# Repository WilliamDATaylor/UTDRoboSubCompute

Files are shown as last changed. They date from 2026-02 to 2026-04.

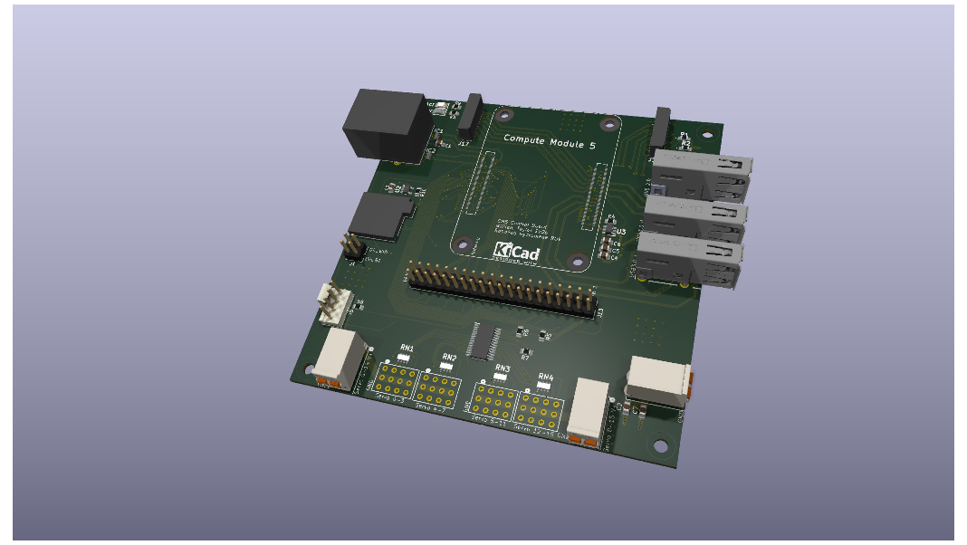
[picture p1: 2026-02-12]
UTDRoboSubCompute.png

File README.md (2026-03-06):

# UTDRoboSubCompute2026
Raspberry PI CM5 carrier board designed for the University of Texas at Dallas' ROV team, [RoboSub](https://utdrobosub.org/).

This will compete in the [2026 MateROV competition](https://materovcompetition.org/).

KiCad 3D render of the PCB

Kicad PCB View

Designs are heavily influenced by the reference RPI CM5 IO board.

[CM5 IO Board Datasheet](https://pip-assets.raspberrypi.com/categories/1097-raspberry-pi-compute-module-5-io-board/documents/RP-008182-DS-2-cm5io-datasheet.pdf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)

[CM5 IO Board KiCad Files](https://pip.raspberrypi.com/categories/1098-design-files)

[CM5 Datasheet](https://pip-assets.raspberrypi.com/categories/944-raspberry-pi-compute-module-5/documents/RP-008180-DS-6-cm5-datasheet.pdf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)

## Documentation Overview: 

### Table of Contents:

1. [Servo Controller](#servo-i2c-controller)
2. [GPIO Pins](#general-purpose-input-output-gpio)
3. [CSI/DSI](#csidsi-connectors)
4. [SD Card boot](#sd-cardtrans-flash-boot)
5. [Power Inputs](#power)
6. [USB 2.0](#usb-20)
7. [USB 3.0](#usb-30)
8. [CM5](#cm5)
9. [Fan](#fan)
10. [Sizing and dimensions](#sizing-and-dimensions)
11. [Trace Routing](#trace-routing)
12. [Additional Details](#additional-details)

### Servo (I<sup>2</sup>c) Controller: 
KiCad Schematic for Servo Controller

Manufacturer: NXP

IC: PCA9685PW, 118

I<sup>2</sup>c Connection: 

Internally connected to GPIO 2 & GPIO 3 (I<sup>2</sup>c1). Info [here](pinout.xyz/pinout/i2c)

The Servo controller is on the x0 I<sup>2</sup>c address

#### Connecting Servos 
KiCad Schematic for Servo header connections
The servos are seperated into two groups of 8 servos for a total of 16 servos. Each group is connected to its own dedicated power input. The pins are just a standard array of 2.54 mm pitch headers. Each servo "bank" (a set of 4 servos) has a dedicated resistor network for the PWM output. 

The max current draw for each set of servo "banks" is *5A*. Realistically, the servos will draw a fraction of this during normal usage, but peaks could be high enough for it to matter. The traces were calibrated for these servos:

[Servos Injora 35KG Brushless Servos](https://www.amazon.com/dp/B0B56SN46D)

[Back to Top](#documentation-overview)

### General Purpose Input Output (GPIO)
KiCad Schematic for 40-Pin GPIO Header

The board uses standard RPI GPIO pin outs.
[GPIO Documentation](https://pinout.xyz/pinout/)

Details about the GPIO for the CM5 can be found on page 12 of the manual.
Probably obvious, but it does need to be said: "Don’t exceed 50 mA for total current load on all 28 GPIO pins."

[Back to Top](#documentation-overview)

### CSI/DSI Connectors
KiCad Schematic for Dual CSI connectors

Manufacturer: Hirose Electric

Model Number: FH12-22S-0.5SH(55) 

Both CSI connectors are configured to be enabled out of the box (deviating from the CM5 design). This may break some HAT compatibility because the CSI1 uses the I<sup>2</sup>c lines normally used for identifying HATs (see pages 10 & 11 of the CM5 docs). Additionally, this will prevent GPIO 0 & 1 from being used as regular pins. (It is entirely possible that this will not cause issues, but your mileage may vary.)
Both connectors are usable as DSI connectors as well. 

[Back to Top](#documentation-overview)

### Ethernet
KiCad Schematic for ethernet connectivity

Manufacturer: ABRACON

Model Number: ARJM11B1-502-NN-EW2 

The CM5 supports 1 gigabit ethernet. An Ethernet jack with magnetics was used to improve signal integrity.
Our specific use case specifically prohibits the use of POE, so its addition would be unnecessary; thus, the board lacks POE compatibility. 

Two ESD protection diodes were used to minimize the impact of static. Our use case necessitates long cable runs, making this a possible issue. 

IC: TPD4E05U06QDQARQ1
Manufacturer: Texas Instraments

[Back to Top](#documentation-overview)

### SD card/TransFlash boot
KiCad Schematic for SD Card
Connector:

Manufacturer: Amphenol

Model Number: GTFP08432B1HR 

Power IC:

Manufacturer: Richtek

Model Number: RT9742GGJ5

This will only work when a CM5 Lite board is in use; if a non-Lite CM5 is used, this can be omitted. 

[Back to Top](#documentation-overview)

### Power
KiCad Schematic for the wago power connectors

As previously mentioned, the voltage for the servos is divided to accommodate differing servo voltages. 

The connectors themselves were chosen for their ease of connection and high power rating (10A at 300V).

Connector: 

Manufacturer: Wago

Model Number: 2091-1372

[Back to Top](#documentation-overview)

### USB 2.0
KiCad Schematic for USB 2.0

Connector: GSB191217FHR

Manufacturer: Amphenol

The USB 2.0 port uses repurposed data lines originally used for USB OTG. As a result of this change, the following must be added to the ```config.txt``` file:

```dtoverlay=dwc2,dr_mode=host```

For more information, review page 8 in the CM5 Documentation.

The USB 3.0 and 2.0 ports share a current regulator that provides up to 2.1 A across all three ports.

IC: AP22653W6-7

Manufacturer: Diodes Inc.

[Back to Top](#documentation-overview)

### USB 3.0
![KiCad Schematic of USB 3.0 Ports](https://pics.wdat-homelab.xyz/u/CMJG52.png)

USB 3.0_1 is P/N swapped to avoid using vias or messy fanouts 

As previously mentioned, the USB ports share a current regulator. 

[Back to Top](#documentation-overview)

### CM5
![KiCad Schematic for Amphenol FFC Connectors for CM5](https://pics.wdat-homelab.xyz/u/SphRqF.png)

The CM5 is placed with the wireless antenna pointing inward. As this is meant to be installed inside a solid aluminum chassis and several meters underwater, Wi-Fi and Bluetooth connectivity have been disregarded. Further, the CM5 that we tested with does not support wireless, so your mileage may vary.

There is an included disable wifi/bluetooth header if necessary for testing.

[Back to Top](#documentation-overview)

### Fan
![KiCad Schematic for Fan Header](https://pics.wdat-homelab.xyz/u/2RXl0h.png)

Optional fan header. The schematic uses a generic PC fan header, but any pins with 2.54 mm pitch will work.

Max power draw: 12w 

[Back to Top](#documentation-overview)

### Sizing and Dimensions

The PCB itself is roughly a 100mm x 100mm square (real value 100mm x 100.08mm), with four M3 mounting holes 92mm center offset.

![PCB Dimensions](https://pics.wdat-homelab.xyz/u/7AKzme.png)

A 3D model has been included in this GitHub repository for reference. 

[Back to Top](#documentation-overview)

### Trace Routing

#### Board Specifications 
Copper Weight: 1 oz 

Layers: 4
 - Signaling
 - Upper Ground Plane
 - Lower Ground Plane
 - Signaling & Power

Manufacturer: JLCPCB

Dialectric: FR4 TG135

Signal Trace Spacing: 3\*width

#### Differnetial Impedence Controlled Signals
There are four major signaling standards used on this board that required controlled impedence in some form. They are:

 - USB 3.0: 90Ω
 - USB 2.0: 90Ω
 - Ethernet: 100Ω
 - MIPI (CSI/DSI): 100Ω

Given the overlap between the standards, the choices for spacing, width, and clearance were divided into two groups: USB(90Ω) and Ethernet/MIPI(100Ω

Dialectric Constant: 4.5
Height: 0.2mm

**Ethernet & MIPI**
 - Trace Width: 0.2mm
 - Trace Spacing: 0.1016mm (4 mils)
 - Z(odd): 50.7457Ω

**USB 3.0/USB 2.0**
 - Trace Width: 0.268 mm
 - Trace Spacing: 0.1016mm (4 mils)
 - Z(odd): 45.0396Ω

All differential traces were given a clearance standard of 4-5 Width of clearance (exluding IC escape). 

[Back to Top](#documentation-overview)

### Additional Details

Additional SMD pads for optional bulk capacitors have been added to the design if issues arise. All SMD components are 0805

During assembly, it is highly recommended to use the included interactive BOM (ibom.html).

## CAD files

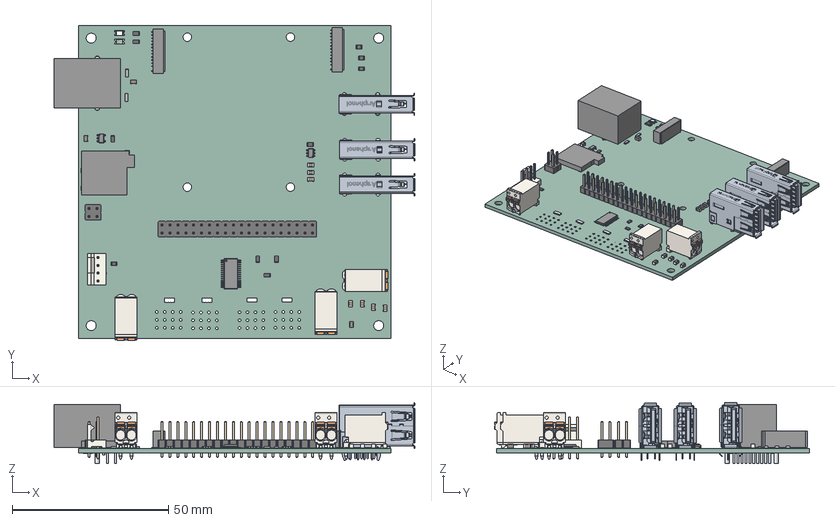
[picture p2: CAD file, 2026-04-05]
cm5testcarrier.step
115.5 x 100.7 x 19.6 mm
CAT16-2200F4LF x 4
C_0805_2012Metric x 10
cm5testcarrier 1.4.1
R_0805_2012Metric x 8
Pins x 3
USB3_HOUSING_14__10_2_1 x 2
PRT0010_3_1 x 2
PRT0011_2_1 x 2
PRT0012_2_1 x 2
PRT0013_2_1 x 2
PRT0014_2_1 x 2
PRT0015_2_1 x 2
PRT0016_2_1 x 2
PRT0017_2_1 x 2
PRT0018_2_1 x 2
USB2_HOUSING_11__17_1_1 x 2
UPRIGHT_SHELL_5__16_9_1 x 2
PRT0019_1_1 x 2
solidBody x 3
Terminal x 3
solidTop x 3
TPD4E05U06QDQARQ1 x 2
PinHeader_2x02_P2.54mm_Vertical
PinHeader_2x20_P2.54mm_Vertical
150120RS75000
PinsArrayLR x 2
PinsArrayL
PinsArrayR
FanPinHeader_1x04_P2.54mm_Vertical
housing
marking x 2
cover
base x 2
Lugs
Leads
UTDRoboSubCompute_PCB

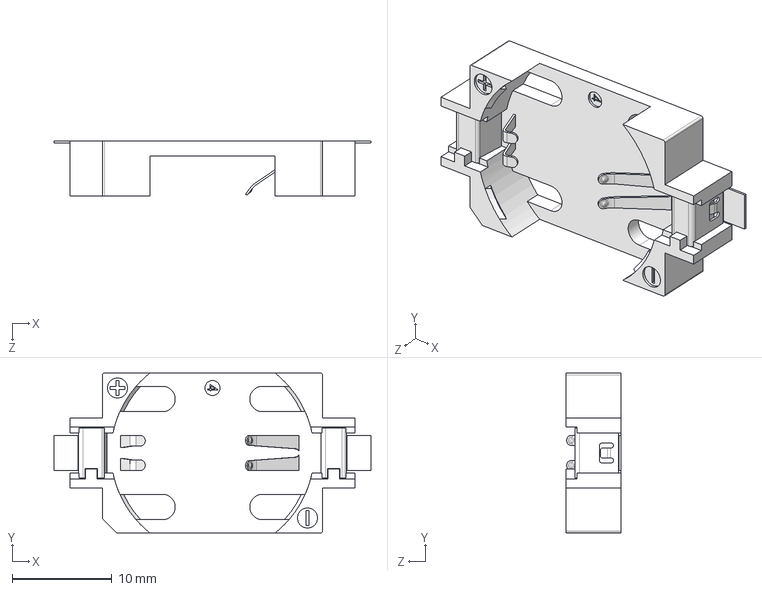
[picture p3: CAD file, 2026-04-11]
RoboSubCompute.models/BAT-HLD-013-SMT-TR.stp
31.7 x 16.0 x 5.50 mm

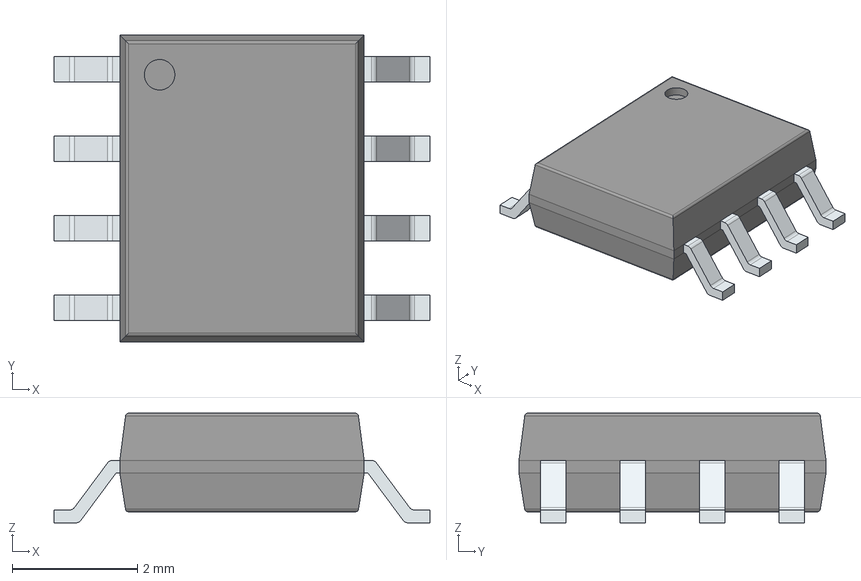
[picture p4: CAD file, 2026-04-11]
RoboSubCompute.models/NE555DR.stp
6.00 x 4.90 x 1.75 mm
PinsArrayLR

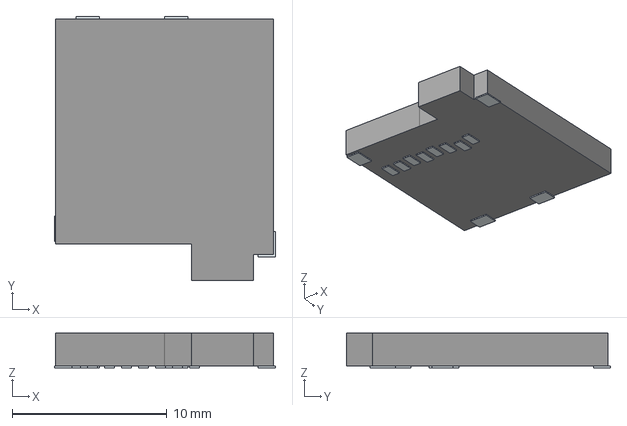
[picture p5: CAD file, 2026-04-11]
RoboSubCompute.models/GTFP08432B1HR.stp
14.3 x 17.1 x 2.23 mm
Pins

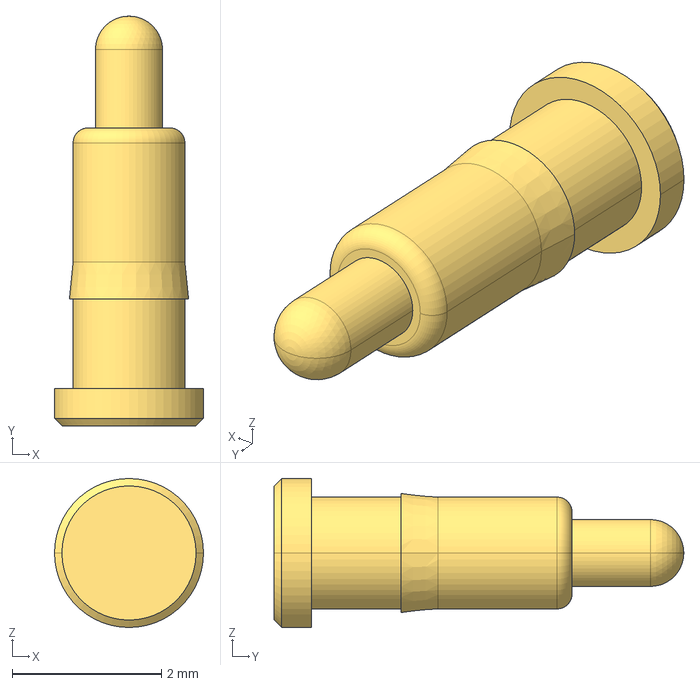
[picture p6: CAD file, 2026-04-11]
RoboSubCompute.models/P70-1020045R.stp
2.00 x 5.50 x 2.00 mm

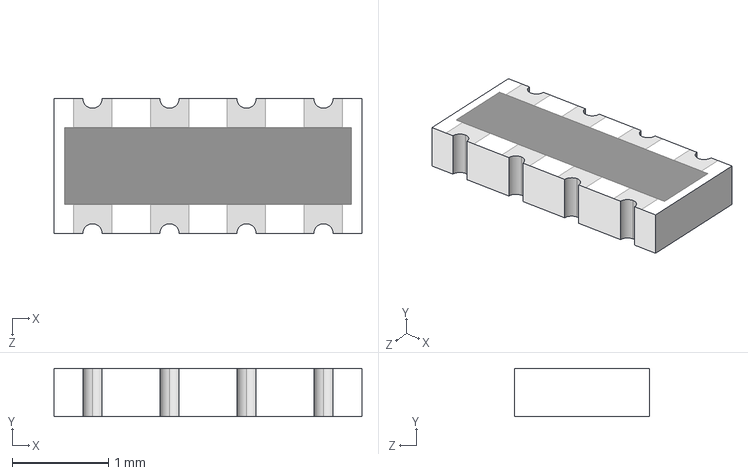
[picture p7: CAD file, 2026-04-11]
RoboSubCompute.models/CAT16-2200F4LF.stp
3.20 x 0.5 x 1.40 mm

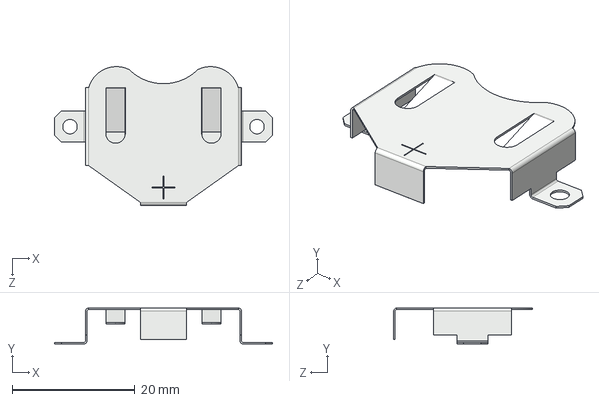
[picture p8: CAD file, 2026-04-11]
RoboSubCompute.models/3008TR.stp
35.5 x 5.84 x 22.6 mm

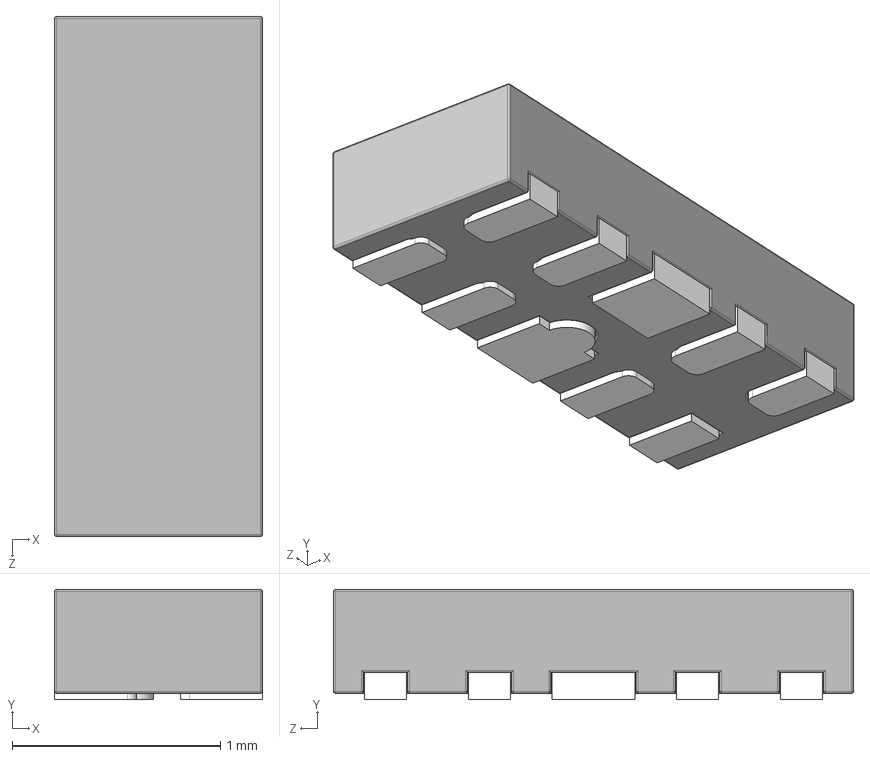
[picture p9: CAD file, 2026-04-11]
RoboSubCompute.models/TPD4E05U06QDQARQ1.stp
1.00 x 0.53 x 2.50 mm

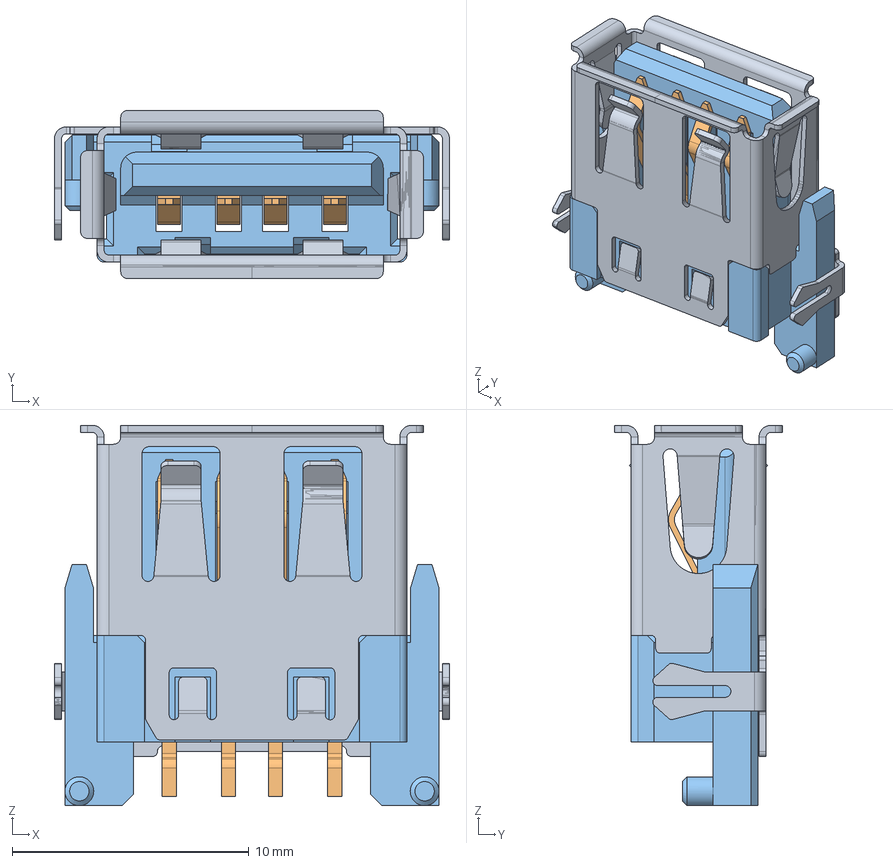
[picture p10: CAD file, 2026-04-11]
RoboSubCompute.models/USB1055-GF-L-A.stp
16.7 x 7.12 x 16.1 mm
USB1055-GF-L-A_PART8
USB1055-GF-L-A_PART7
USB1055-GF-L-A_PART6
USB1055-GF-L-A_PART5
USB1055-GF-L-A_PART4
USB1055-GF-L-A_PART3
USB1055-GF-L-A_PART2
USB1055-GF-L-A_PART1

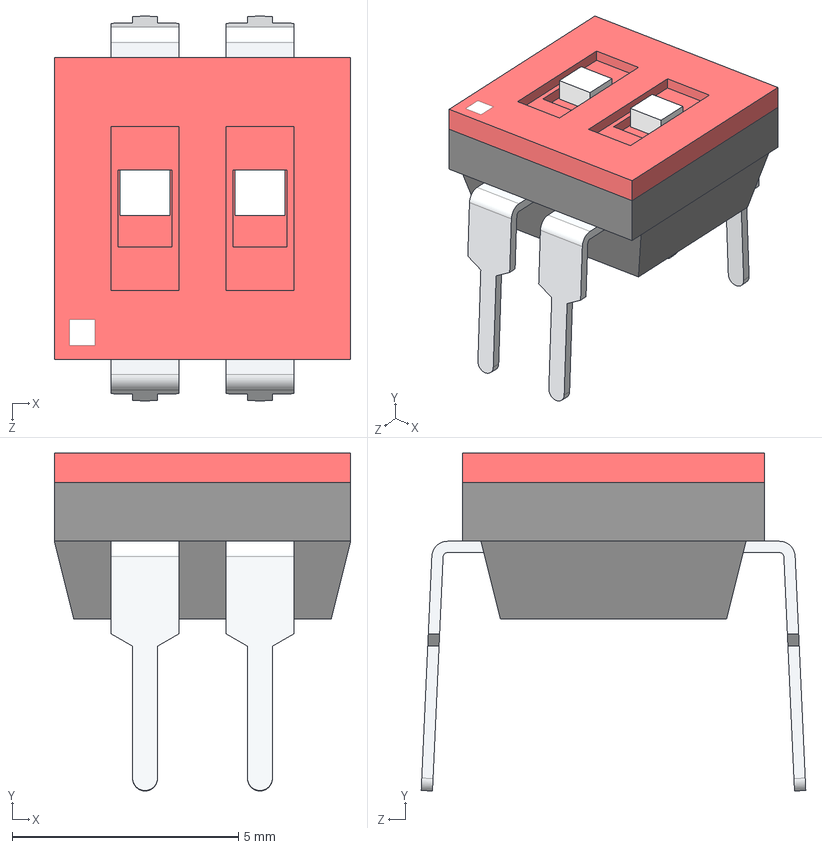
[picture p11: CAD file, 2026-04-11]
RoboSubCompute.models/SD02H0B.stp
6.55 x 7.47 x 8.50 mm

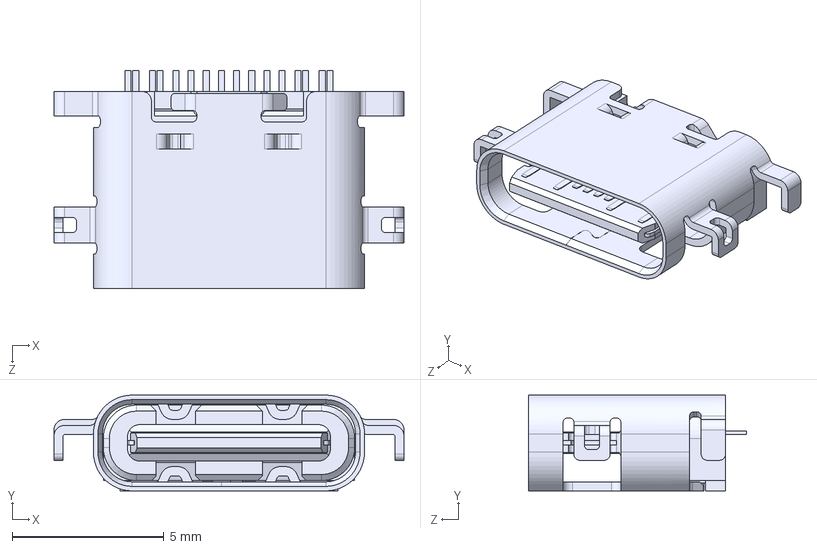
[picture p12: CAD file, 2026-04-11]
RoboSubCompute.models/UJ20-C-H-G-MSMT-4-P16-TR.stp
11.5 x 3.16 x 7.20 mm

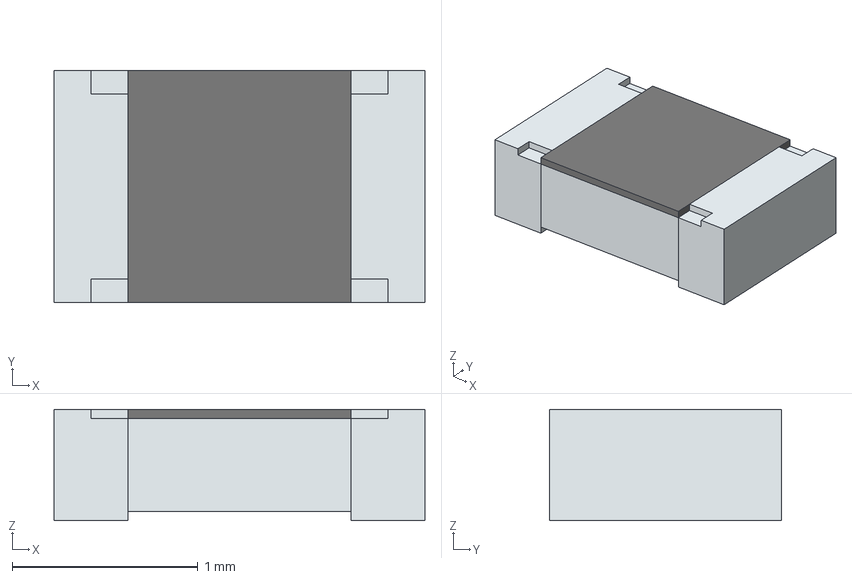
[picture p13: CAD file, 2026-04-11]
RoboSubCompute.models/ERJ-U06D2201V.stp
2.00 x 1.25 x 0.6 mm
solidBody
Terminal
solidTop

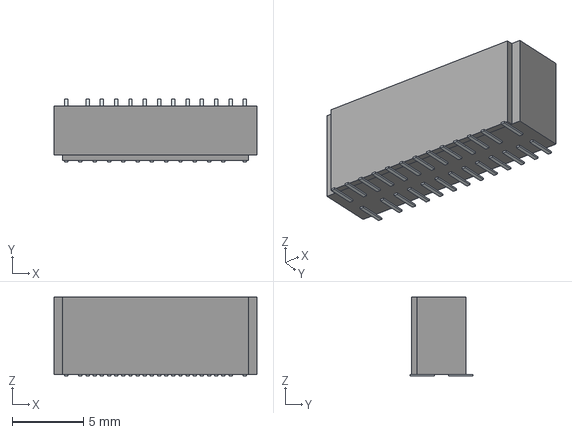
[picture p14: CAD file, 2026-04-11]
RoboSubCompute.models/TF38-22S-0.5SV_830_.stp
14.2 x 4.44 x 5.50 mm
Pins

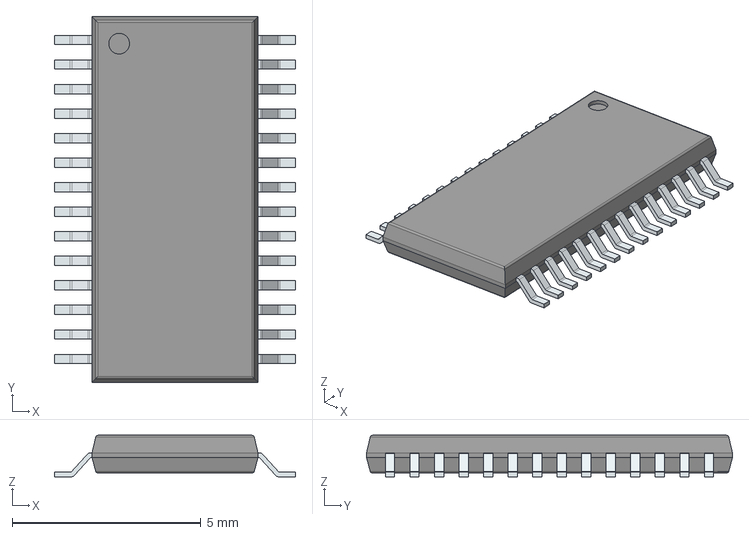
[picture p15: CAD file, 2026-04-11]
RoboSubCompute.models/PCA9685PW,118.stp
6.40 x 9.70 x 1.10 mm
PinsArrayLR

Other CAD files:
RoboSubCompute.models/RT9742GGJ5.stp
RoboSubCompute.models/ARJM11B1-502-NN-EW2.stp
RoboSubCompute.models/2091-1372.stp
RoboSubCompute.models/cm5.conn.stp
RoboSubCompute.models/10164227-1001A1RLF.stp
RoboSubCompute.models/150120GS75000.stp
RoboSubCompute.models/150120RS75000.stp
RoboSubCompute.models/1663962.stp
RoboSubCompute.models/AP22653W6-7.step
RoboSubCompute.models/AP22653W6-7.stp
RoboSubCompute.models/Ethernet.stp
RoboSubCompute.models/GSB191217FHR.stp
RoboSubCompute.models/GSB3112311HR.stp
RoboSubCompute.models/GSB3116344KHHR.stp
RoboSubCompute.models/csi connector.stp

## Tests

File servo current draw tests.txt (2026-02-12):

INJORA INJS235 35KG Waterproof Brushless servo motor 
idle power consumption 3mA
180 degree range 

### 8.4v

peak current draw at 0 to 180 : 2.1 A

### gradual sweeps:

10 degree delta 
200ms delay
current draw : 250mA

1 degree delta
20ms delay
current draw: 150mA

30 degree delta 
200ms delay 
current: 700mA 

60 degree delta
200ms delay 
current: 1.2A

10 degree delta: 
50ms delay
current: 600mA

20 degree delta
50ms delay
current: 1.3A

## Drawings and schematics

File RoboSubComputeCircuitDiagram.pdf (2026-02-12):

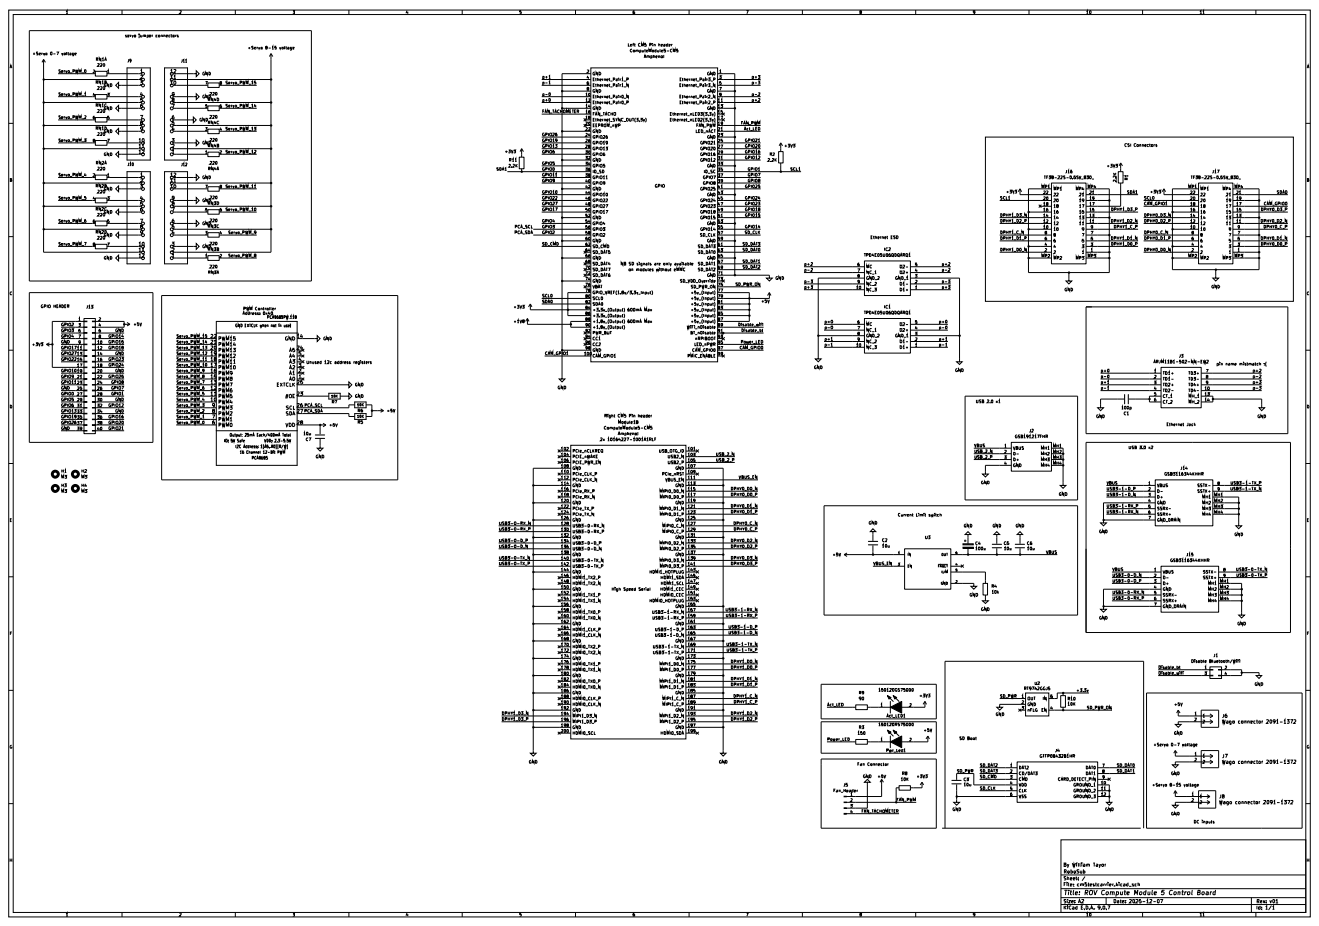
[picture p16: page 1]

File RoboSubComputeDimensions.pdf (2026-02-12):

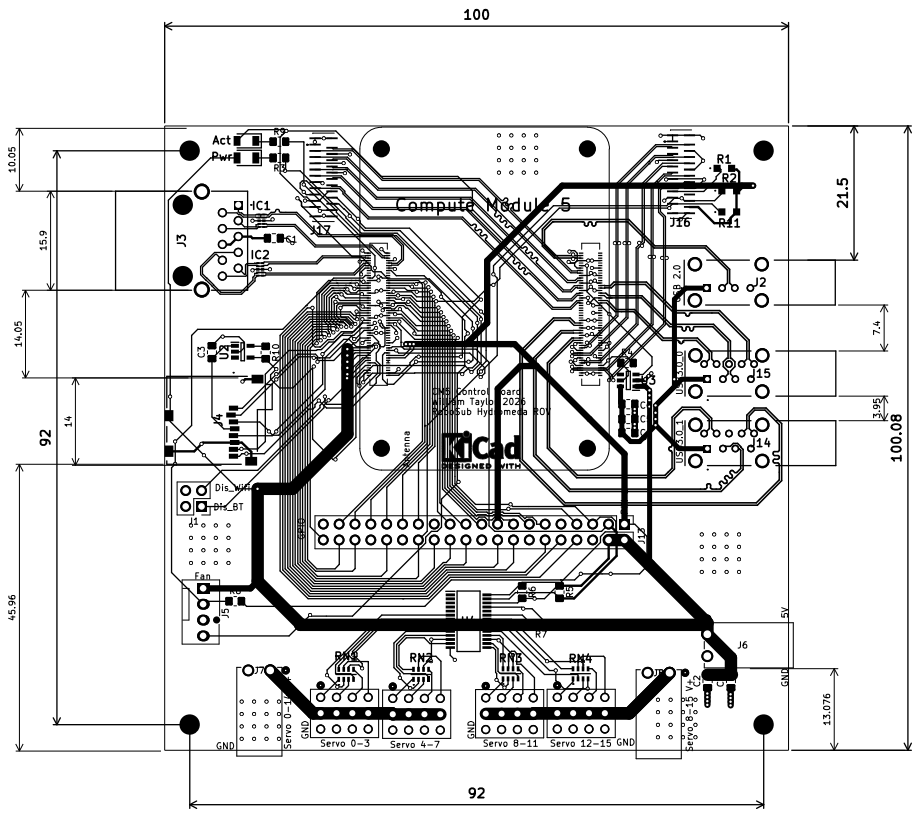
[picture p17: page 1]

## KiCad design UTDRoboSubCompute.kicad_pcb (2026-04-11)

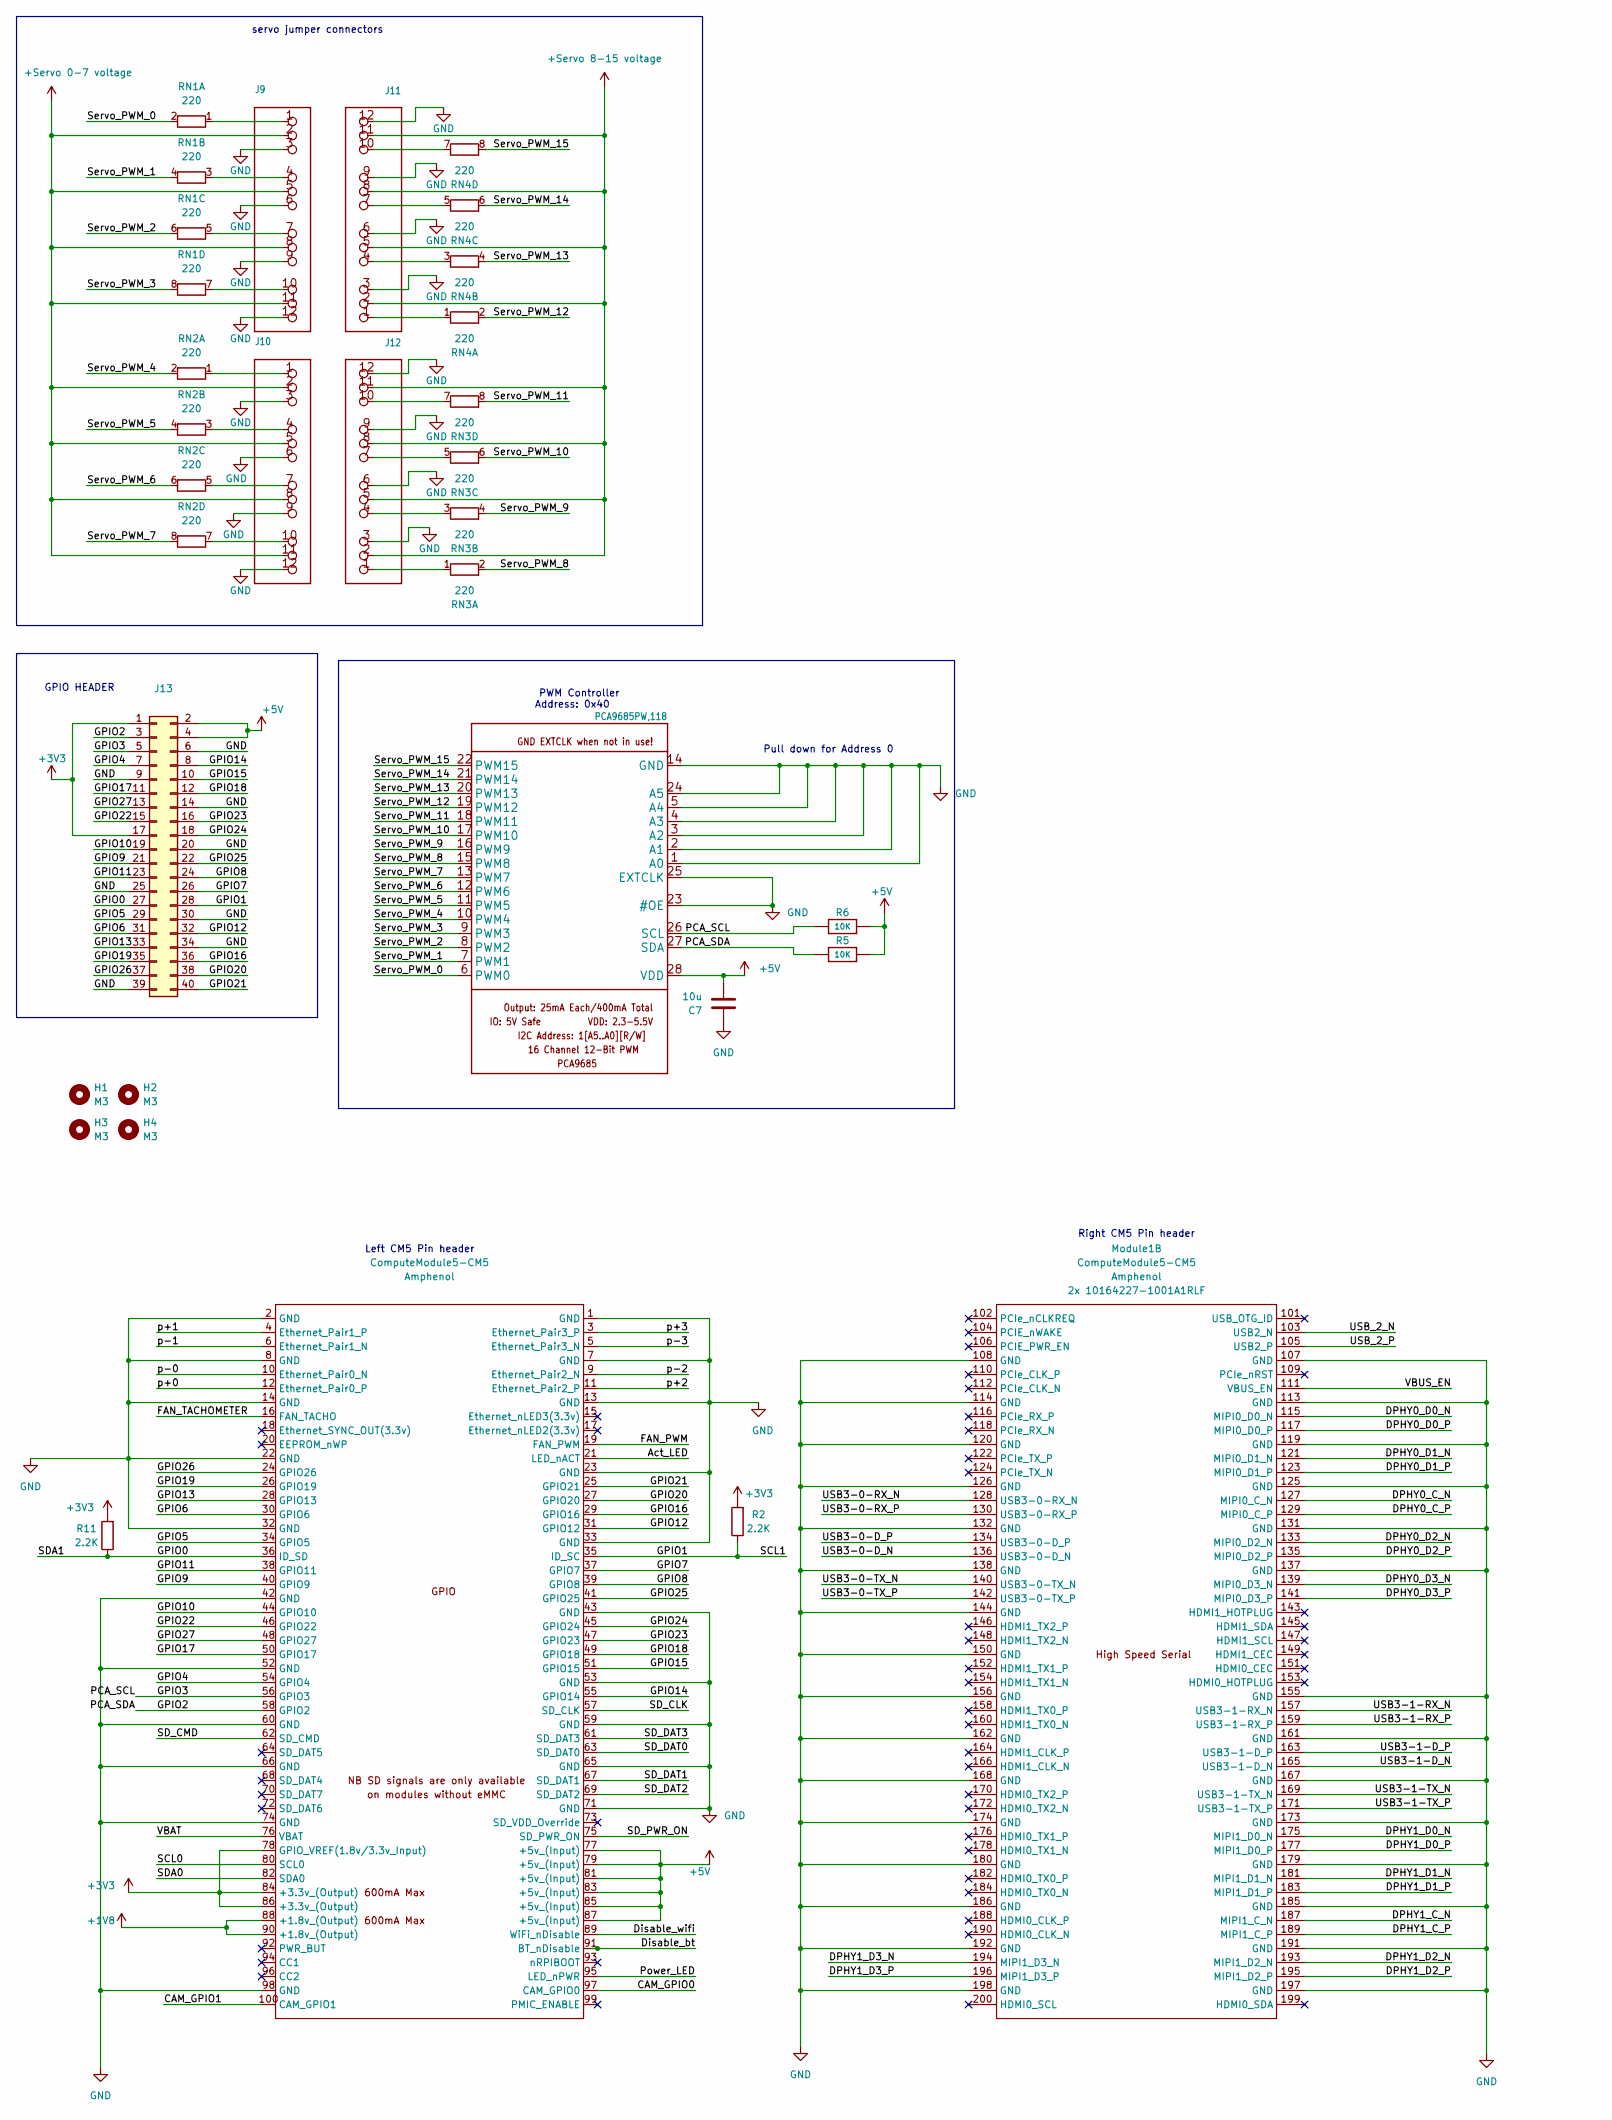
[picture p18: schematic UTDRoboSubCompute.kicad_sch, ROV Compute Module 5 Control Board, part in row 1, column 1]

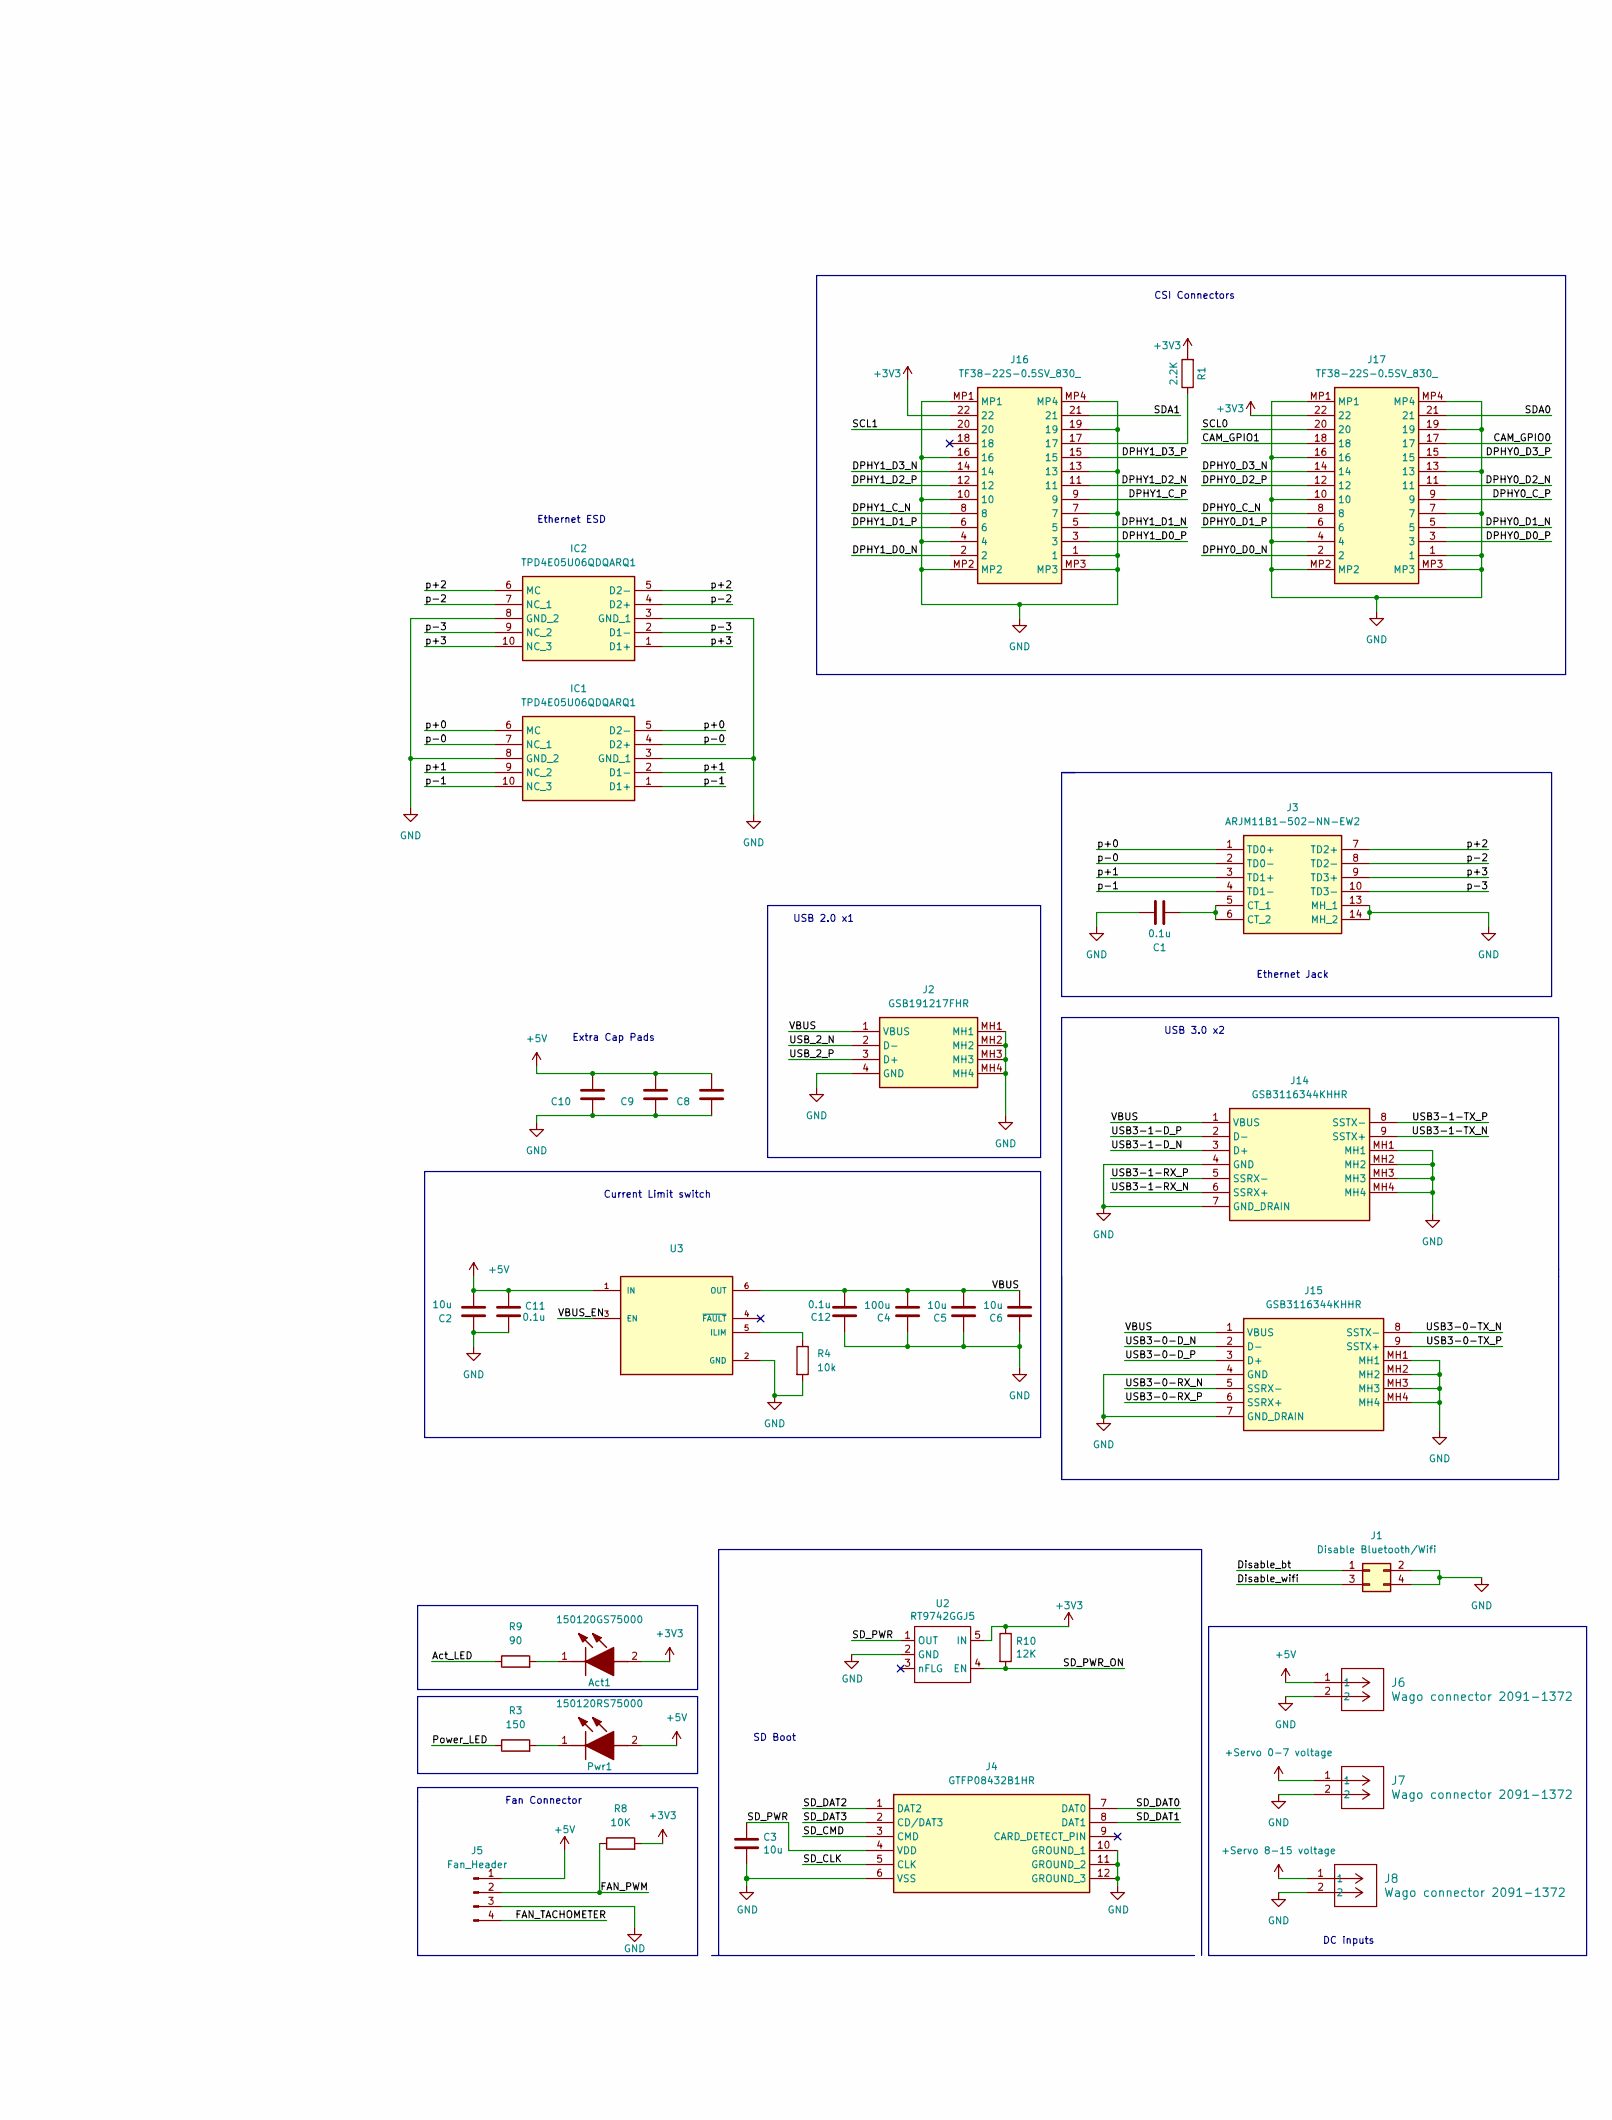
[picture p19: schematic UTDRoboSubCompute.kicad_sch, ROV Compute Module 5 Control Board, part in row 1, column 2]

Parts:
Act1: 150120GS75000; LEDC3214X68N; Mouser Part Number 710-150120GS75000
C1: 0.1u; C_0805_2012Metric_Pad1.18x1.45mm_HandSolder; Mouser Part Number 581-08055C101K
C2, C7: 10u; C_0805_2012Metric_Pad1.18x1.45mm_HandSolder; Mouser Part Number 581-08056D106K
C3, C5, C6: 10u; C_0805_2012Metric_Pad1.18x1.45mm_HandSolder; Part Description 10uF 10% 10V Ceramic Capacitor X7R 0805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; Mouser Part Number 581-08056D106K
C4: 100u; C_0805_2012Metric_Pad1.18x1.45mm_HandSolder; Part Description Capacitor, SP-Cap, 100u, 6.3V, 15mR ESR; Mouser Part Number 963-JMK325BJ107MM-T
C8, C9, C10: C_0805_2012Metric_Pad1.18x1.45mm_HandSolder; Mouser Part Number 581-08056D106K
C11, C12: 0.1u; C_0805_2012Metric_Pad1.15x1.40mm_HandSolder; Mouser Part Number 581-08055C101K
H1, H2, H3, H4: M3; MountingHole_3.2mm_M3
IC1, IC2: TPD4E05U06QDQARQ1; DQA_R-PUSON-N10_; Mouser Part Number 595-PD4E05U06QDQARQ1
J1: Disable Bluetooth/Wifi; PinHeader_2x02_P2.54mm_Vertical
J2: GSB191217FHR; Mouser Part Number 523-GSB191217FHR
J3: ARJM11B1-502-NN-EW2; ARJM11B1502NNEW2; Mouser Part Number 815-RJM11B1502NNEW2
J4: GTFP08432B1HR; Mouser Part Number 523-GTFP08432B1HR
J5: Fan_Header; FanPinHeader_1x04_P2.54mm_Vertical
J6, J7, J8: Wago connector 2091-1372; CONN2_2091-1372_WAGO; Mouser Part Number DigiKey
J9, J10, J11, J12: HEADER-3X04; CON12_3X4_TU_TSW_SAI
J13: Conn_02x20_Odd_Even; PinHeader_2x20_P2.54mm_Vertical; Mouser Part Number 798-FH12-22S-0.5SH55
J14, J15: GSB3116344KHHR; Mouser Part Number 523-GSB3116344KHHR
J16, J17: TF38-22S-0.5SV_830_; TF3822S05SV830; Mouser Part Number 798-TF38-22S-05SV830
Module1: ComputeModule5-CM5; Raspberry-Pi-5-Compute-Module; Mouser Part Number 649-01642271001A1RLF
Pwr1: 150120RS75000; LEDC3216X68N; Mouser Part Number 710-150120RS75000
R1, R2, R11: 2.2K; ERJS06_U06__0805_; Mouser Part Number 667-ERJ-U06D2201V
R3: 150; R_0805_2012Metric_Pad1.20x1.40mm_HandSolder; Mouser Part Number 667-ERJ-UP6D1500V
R4: 10k; R_0805_2012Metric_Pad1.20x1.40mm_HandSolder; Mouser Part Number 667-ERJ-UP6D1002V
R5, R6, R8: 10K; R_0805_2012Metric_Pad1.20x1.40mm_HandSolder; Mouser Part Number 667-ERJ-UP6D1002V
R9: 90; R_0805_2012Metric_Pad1.20x1.40mm_HandSolder; Mouser Part Number 667-ERJ-UP6D91R0V
R10: 12K; R_0805_2012Metric_Pad1.20x1.40mm_HandSolder; Part Description Resistor 10K M1005 1% 63mW; Mouser Part Number 603-RP0805FRE0712KL
RN1, RN2, RN3, RN4: 220; CAT161000F4; Mouser Part Number 652-CAT16-2200F4LF
U2: RT9742GGJ5; SOT94P280X100-5N; Part Description Power Switch/Driver 1:1 N-Channel 1A TS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; Mouser Part Number 835-RT9742GGJ5
U3: AP22653W6-7; SOT95P280X145-6N; PARTREV 2-2; Mouser Part Number 621-AP22653W6-7
U4: PCA9685PW,118; SOP65P640X110-28N; Mouser Part Number 771-PCA9685PW,118

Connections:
+1V8: Module1.88 (+1.8v_(Output)), Module1.90 (+1.8v_(Output))
+3V3: Act1.2 (A), J13.1, J13.17, J16.22, J17.22, Module1.78 (GPIO_VREF(1.8v/3.3v_Input)), Module1.84 (+3.3v_(Output)), Module1.86 (+3.3v_(Output)), R1.2, R2.2, R8.2, R10.1, R11.2, U2.5 (IN)
+5V: C2.2, C7.2, C8.2, C9.2, C10.2, C11.2, J5.1, J6.1, J13.2, J13.4, Module1.77 (+5v_(Input)), Module1.79 (+5v_(Input)), Module1.81 (+5v_(Input)), Module1.83 (+5v_(Input)), Module1.85 (+5v_(Input)), Module1.87 (+5v_(Input)), Pwr1.2 (A), R5.1, R6.1, U3.1 (IN), U4.28 (VDD)
+Servo 0-7 voltage: J7.1, J9.2, J9.5, J9.8, J9.11, J10.2, J10.5, J10.8, J10.11
+Servo 8-15 voltage: J8.1, J11.2, J11.5, J11.8, J11.11, J12.2, J12.5, J12.8, J12.11
/Act_LED: Module1.21 (LED_nACT), R9.1
/CAM_GPIO0: J17.17, Module1.97 (CAM_GPIO0)
/CAM_GPIO1: J17.18, Module1.100 (CAM_GPIO1)
/DPHY0_C_N: J17.8, Module1.127 (MIPI0_C_N)
/DPHY0_C_P: J17.9, Module1.129 (MIPI0_C_P)
/DPHY0_D0_N: J17.2, Module1.115 (MIPI0_D0_N)
/DPHY0_D0_P: J17.3, Module1.117 (MIPI0_D0_P)
/DPHY0_D1_N: J17.5, Module1.121 (MIPI0_D1_N)
/DPHY0_D1_P: J17.6, Module1.123 (MIPI0_D1_P)
/DPHY0_D2_N: J17.11, Module1.133 (MIPI0_D2_N)
/DPHY0_D2_P: J17.12, Module1.135 (MIPI0_D2_P)
/DPHY0_D3_N: J17.14, Module1.139 (MIPI0_D3_N)
/DPHY0_D3_P: J17.15, Module1.141 (MIPI0_D3_P)
/DPHY1_C_N: J16.8, Module1.187 (MIPI1_C_N)
/DPHY1_C_P: J16.9, Module1.189 (MIPI1_C_P)
/DPHY1_D0_N: J16.2, Module1.175 (MIPI1_D0_N)
/DPHY1_D0_P: J16.3, Module1.177 (MIPI1_D0_P)
/DPHY1_D1_N: J16.5, Module1.181 (MIPI1_D1_N)
/DPHY1_D1_P: J16.6, Module1.183 (MIPI1_D1_P)
/DPHY1_D2_N: J16.11, Module1.193 (MIPI1_D2_N)
/DPHY1_D2_P: J16.12, Module1.195 (MIPI1_D2_P)
/DPHY1_D3_N: J16.14, Module1.194 (MIPI1_D3_N)
/DPHY1_D3_P: J16.15, Module1.196 (MIPI1_D3_P)
/Disable_bt: J1.1, Module1.91 (BT_nDisable)
/Disable_wifi: J1.3, Module1.89 (WiFi_nDisable)
/FAN_PWM: J5.2, Module1.19 (FAN_PWM), R8.1
/FAN_TACHOMETER: J5.4, Module1.16 (FAN_TACHO)
/GPIO0: J13.27, J16.21, Module1.36 (ID_SD), R11.1
/GPIO1: J13.28, J16.20, Module1.35 (ID_SC), R2.1
/GPIO2: J13.3, Module1.58 (GPIO2), R5.2, U4.27 (SDA)
/GPIO3: J13.5, Module1.56 (GPIO3), R6.2, U4.26 (SCL)
/GPIO4: J13.7, Module1.54 (GPIO4)
/GPIO5: J13.29, Module1.34 (GPIO5)
/GPIO6: J13.31, Module1.30 (GPIO6)
/GPIO7: J13.26, Module1.37 (GPIO7)
/GPIO8: J13.24, Module1.39 (GPIO8)
/GPIO9: J13.21, Module1.40 (GPIO9)
/GPIO10: J13.19, Module1.44 (GPIO10)
/GPIO11: J13.23, Module1.38 (GPIO11)
/GPIO12: J13.32, Module1.31 (GPIO12)
/GPIO13: J13.33, Module1.28 (GPIO13)
/GPIO14: J13.8, Module1.55 (GPIO14)
/GPIO15: J13.10, Module1.51 (GPIO15)
/GPIO16: J13.36, Module1.29 (GPIO16)
/GPIO17: J13.11, Module1.50 (GPIO17)
/GPIO18: J13.12, Module1.49 (GPIO18)
/GPIO19: J13.35, Module1.26 (GPIO19)
/GPIO20: J13.38, Module1.27 (GPIO20)
/GPIO21: J13.40, Module1.25 (GPIO21)
/GPIO22: J13.15, Module1.46 (GPIO22)
/GPIO23: J13.16, Module1.47 (GPIO23)
/GPIO24: J13.18, Module1.45 (GPIO24)
/GPIO25: J13.22, Module1.41 (GPIO25)
/GPIO26: J13.37, Module1.24 (GPIO26)
/GPIO27: J13.13, Module1.48 (GPIO27)
/Power_LED: Module1.95 (LED_nPWR), R3.1
/SCL0: J17.20, Module1.80 (SCL0)
/SDA0: J17.21, Module1.82 (SDA0)
/SD_CLK: J4.5 (CLK), Module1.57 (SD_CLK)
/SD_CMD: J4.3 (CMD), Module1.62 (SD_CMD)
/SD_DAT0: J4.7 (DAT0), Module1.63 (SD_DAT0)
/SD_DAT1: J4.8 (DAT1), Module1.67 (SD_DAT1)
/SD_DAT2: J4.1 (DAT2), Module1.69 (SD_DAT2)
/SD_DAT3: J4.2 (CD/DAT3), Module1.61 (SD_DAT3)
/SD_PWR: C3.1, J4.4 (VDD), U2.1 (OUT)
/SD_PWR_ON: Module1.75 (SD_PWR_ON), R10.2, U2.4 (EN)
/Servo_PWM_0: RN1.2 (R1.2), U4.6 (PWM0)
/Servo_PWM_1: RN1.4 (R2.2), U4.7 (PWM1)
/Servo_PWM_2: RN1.6 (R3.2), U4.8 (PWM2)
/Servo_PWM_3: RN1.8 (R4.2), U4.9 (PWM3)
/Servo_PWM_4: RN2.2 (R1.2), U4.10 (PWM4)
/Servo_PWM_5: RN2.4 (R2.2), U4.11 (PWM5)
/Servo_PWM_6: RN2.6 (R3.2), U4.12 (PWM6)
/Servo_PWM_7: RN2.8 (R4.2), U4.13 (PWM7)
/Servo_PWM_8: RN3.2 (R1.2), U4.15 (PWM8)
/Servo_PWM_9: RN3.4 (R2.2), U4.16 (PWM9)
/Servo_PWM_10: RN3.6 (R3.2), U4.17 (PWM10)
/Servo_PWM_11: RN3.8 (R4.2), U4.18 (PWM11)
/Servo_PWM_12: RN4.2 (R1.2), U4.19 (PWM12)
/Servo_PWM_13: RN4.4 (R2.2), U4.20 (PWM13)
/Servo_PWM_14: RN4.6 (R3.2), U4.21 (PWM14)
/Servo_PWM_15: RN4.8 (R4.2), U4.22 (PWM15)
/USB3-0-D_N: J15.2 (D-), Module1.136 (USB3-0-D_N)
/USB3-0-D_P: J15.3 (D+), Module1.134 (USB3-0-D_P)
/USB3-0-RX_N: J15.5 (SSRX-), Module1.128 (USB3-0-RX_N)
/USB3-0-RX_P: J15.6 (SSRX+), Module1.130 (USB3-0-RX_P)
/USB3-0-TX_N: J15.8 (SSTX-), Module1.140 (USB3-0-TX_N)
/USB3-0-TX_P: J15.9 (SSTX+), Module1.142 (USB3-0-TX_P)
/USB3-1-D_N: J14.3 (D+), Module1.165 (USB3-1-D_N)
/USB3-1-D_P: J14.2 (D-), Module1.163 (USB3-1-D_P)
/USB3-1-RX_N: J14.6 (SSRX+), Module1.157 (USB3-1-RX_N)
/USB3-1-RX_P: J14.5 (SSRX-), Module1.159 (USB3-1-RX_P)
/USB3-1-TX_N: J14.9 (SSTX+), Module1.169 (USB3-1-TX_N)
/USB3-1-TX_P: J14.8 (SSTX-), Module1.171 (USB3-1-TX_P)
/USB_2_N: J2.2 (D-), Module1.103 (USB2_N)
/USB_2_P: J2.3 (D+), Module1.105 (USB2_P)
/VBAT: Module1.76 (VBAT)
/VBUS: C4.2, C5.2, C6.2, C12.2, J2.1 (VBUS), J14.1 (VBUS), J15.1 (VBUS), U3.6 (OUT)
/VBUS_EN: Module1.111 (VBUS_EN), U3.3 (EN)
/p+0: IC1.5 (D2-), IC1.6 (MC), J3.1 (TD0+), Module1.12 (Ethernet_Pair0_P)
/p+1: IC1.2 (D1-), IC1.9 (NC_2), J3.3 (TD1+), Module1.4 (Ethernet_Pair1_P)
/p+2: IC2.5 (D2-), IC2.6 (MC), J3.7 (TD2+), Module1.11 (Ethernet_Pair2_P)
/p+3: IC2.1 (D1+), IC2.10 (NC_3), J3.9 (TD3+), Module1.3 (Ethernet_Pair3_P)
/p-0: IC1.4 (D2+), IC1.7 (NC_1), J3.2 (TD0-), Module1.10 (Ethernet_Pair0_N)
/p-1: IC1.1 (D1+), IC1.10 (NC_3), J3.4 (TD1-), Module1.6 (Ethernet_Pair1_N)
/p-2: IC2.4 (D2+), IC2.7 (NC_1), J3.8 (TD2-), Module1.9 (Ethernet_Pair2_N)
/p-3: IC2.2 (D1-), IC2.9 (NC_2), J3.10 (TD3-), Module1.5 (Ethernet_Pair3_N)
GND: C1.1, C2.1, C3.2, C4.1, C5.1, C6.1, C7.1, C8.1, C9.1, C10.1, C11.1, C12.1, IC1.3 (GND_1), IC1.8 (GND_2), IC2.3 (GND_1), IC2.8 (GND_2), J1.2, J1.4, J2.4 (GND), J2.MH1, J2.MH2, J2.MH3, J2.MH4, J3.13 (MH_1), J3.14 (MH_2), J4.6 (VSS), J4.10 (GROUND_1), J4.11 (GROUND_2), J4.12 (GROUND_3), J5.3, J6.2, J7.2, J8.2, J9.3, J9.6, J9.9, J9.12, J10.3, J10.6, J10.9, J10.12, J11.3, J11.6, J11.9, J11.12, J12.3, J12.6, J12.9, J12.12, J13.6, J13.9, J13.14, J13.20, J13.25, J13.30, J13.34, J13.39, J14.4 (GND), J14.7 (GND_DRAIN), J14.MH1, J14.MH2, J14.MH3, J14.MH4, J15.4 (GND), J15.7 (GND_DRAIN), J15.MH1, J15.MH2, J15.MH3, J15.MH4, J16.1, J16.4, J16.7, J16.10, J16.13, J16.16, J16.19, J16.MP1, J16.MP2, J16.MP3, J16.MP4, J17.1, J17.4, J17.7, J17.10, J17.13, J17.16, J17.19, J17.MP1, J17.MP2, J17.MP3, J17.MP4, Module1.1 (GND), Module1.2 (GND), Module1.7 (GND), Module1.8 (GND), Module1.13 (GND), Module1.14 (GND), Module1.22 (GND), Module1.23 (GND), Module1.32 (GND), Module1.33 (GND), Module1.42 (GND), Module1.43 (GND), Module1.52 (GND), Module1.53 (GND), Module1.59 (GND), Module1.60 (GND), Module1.65 (GND), Module1.66 (GND), Module1.71 (GND), Module1.74 (GND), Module1.98 (GND), Module1.107 (GND), Module1.108 (GND), Module1.113 (GND), Module1.114 (GND), Module1.119 (GND), Module1.120 (GND), Module1.125 (GND), Module1.126 (GND), Module1.131 (GND), Module1.132 (GND), Module1.137 (GND), Module1.138 (GND), Module1.144 (GND), Module1.150 (GND), Module1.155 (GND), Module1.156 (GND), Module1.161 (GND), Module1.162 (GND), Module1.167 (GND), Module1.168 (GND), Module1.173 (GND), Module1.174 (GND), Module1.179 (GND), Module1.180 (GND), Module1.185 (GND), Module1.186 (GND), Module1.191 (GND), Module1.192 (GND), Module1.197 (GND), Module1.198 (GND), R4.2, U2.2 (GND), U3.2 (GND), U4.1 (A0), U4.2 (A1), U4.3 (A2), U4.4 (A3), U4.5 (A4), U4.14 (GND), U4.23 (#OE), U4.24 (A5), U4.25 (EXTCLK)
unnamed: Act1.1 (K), R9.2
unnamed: C1.2, J3.5 (CT_1), J3.6 (CT_2)
unnamed: J16.17, R1.1
unnamed: Pwr1.1 (K), R3.2
unnamed: J9.1, RN1.1 (R1.1)
unnamed: J9.4, RN1.3 (R2.1)
unnamed: J9.7, RN1.5 (R3.1)
unnamed: J9.10, RN1.7 (R4.1)
unnamed: J10.1, RN2.1 (R1.1)
unnamed: J10.4, RN2.3 (R2.1)
unnamed: J10.7, RN2.5 (R3.1)
unnamed: J10.10, RN2.7 (R4.1)
unnamed: J12.1, RN3.1 (R1.1)
unnamed: J12.4, RN3.3 (R2.1)
unnamed: J12.7, RN3.5 (R3.1)
unnamed: J12.10, RN3.7 (R4.1)
unnamed: J11.1, RN4.1 (R1.1)
unnamed: J11.4, RN4.3 (R2.1)
unnamed: J11.7, RN4.5 (R3.1)
unnamed: J11.10, RN4.7 (R4.1)
unnamed: R4.1, U3.5 (ILIM)

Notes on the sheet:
PWM Controller
Extra Cap Pads
Right CM5 Pin header
Current Limit switch
Fan Connector
CSI Connectors
Ethernet ESD
servo jumper connectors
USB 2.0 x1
Ethernet Jack
DC inputs
GPIO HEADER
SD Boot
Pull down for Address 0
Address: 0x40
USB 3.0 x2
Left CM5 Pin header

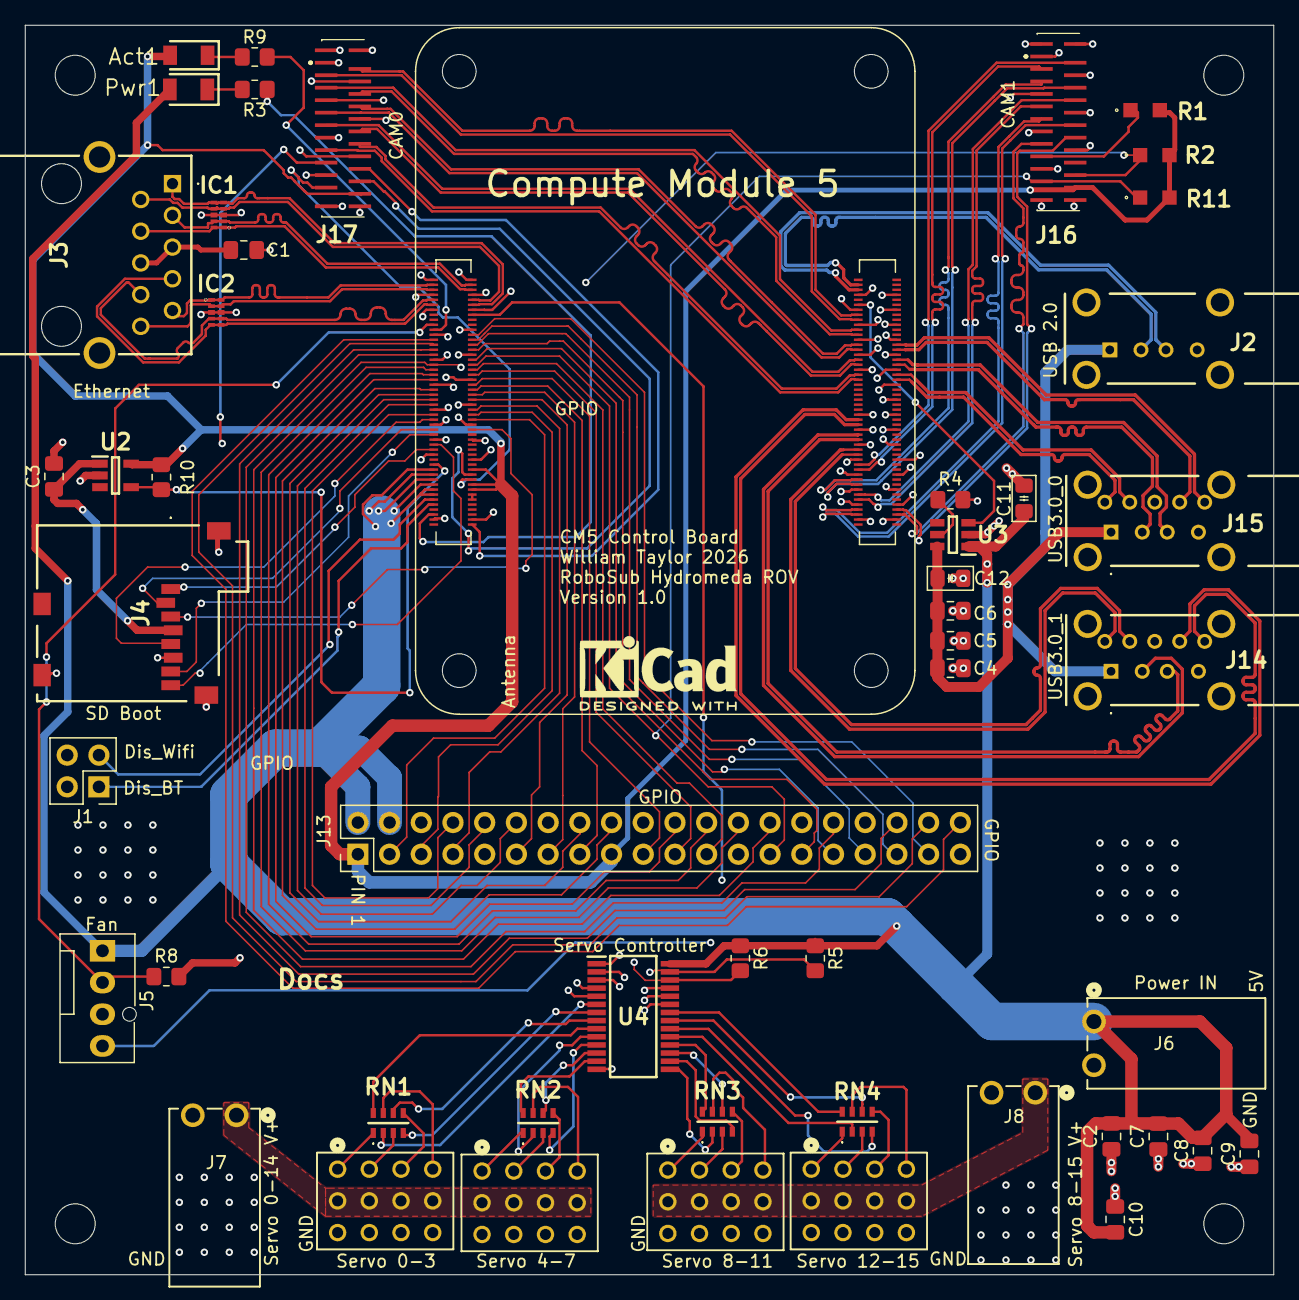
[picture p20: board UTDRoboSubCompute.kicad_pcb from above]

Board: 4 copper layers, 100.0 x 100.1 mm, 55 parts (0 on the bottom side), 133 nets.

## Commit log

2025-10-31 Added USB 3.0 ports & added VBUS current reg
    Found a newer version of the USB current limiter so I implemented that.
    Added USB 3.0 ports and reorganized some nets a bit
    [cm5testcarrier.kicad_sch]
2025-11-17 Servo Controller Finished miscs things reorganized
    - implemented Servo Controller
    - split servo voltage supplies
    - corrected gpio connections
    - implemented fan connector
    - made the usb 2.0 more tidy
    - cleaned up pin nets
    [Adafruit PCA9685 rev C.brd, Adafruit PCA9685 rev C.kicad_sch, Adafruit PCA9685 rev C.sch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]
2025-12-05 Updated footprints & reorganized file structure
    - changed footprints to hand solderable sizes
    - made the file structure make more sense
    - removed files that were not needed in the project
    [2091-1372.stp, AP22653W6-7.step, Adafruit PCA9685 rev C.brd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]
2026-01-20 Add CSI connector footprint, symbol, and model
    - Partially routed USB 3.0
    - routed ethernet
    - added LEDs
    - updated BOM
    - switched passives to 0805 to save space
    - added CSI/DSI ports (still unrouted)
    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
    [cm5testcarrier.kicad_pcb, cm5testcarrier.kicad_sch, csi connector.stp]
2026-02-12 V1 Done
    - finished routing traces
    - filled ground planes
    - started readme documentation
    - resized power traces for power needs
    - relocated the servo setup to allow for better placement of the GPIO
    - relocated some ports for better diff pair routing
    - swapped cm5 board orientation for better routing (also doesn't matter because wireless will be unused)
    [cm5testcarrier.dsn, cm5testcarrier.kicad_pcb, cm5testcarrier.kicad_sch]
2026-02-12 Updated Name
    Renamed all files referencing cm5 test board to be UTDRoboSubCompute since we're going forward with this design
    [UTDRoboSubCompute.kicad_pcb, UTDRoboSubCompute.kicad_sch, cm5testcarrier.dsn]
2026-02-21 Improve README and update PCB sheet/net refs
    Expanded and clarified README: added table of contents, more component details (servo, CSI/DSI, Ethernet, USB, SD boot, power, fan), images, USB config hint (dtoverlay), PCB dimensions, and a recommendation to use the interactive BOM. Updated UTDRoboSubCompute.kicad_pcb: replaced many sheetfile references from cm5testcarrier.kicad_sch to UTDRoboSubCompute.kicad_sch, ), adjusted a pad reference, and refreshed numerous footprint UUIDs. These changes align documentation with the board files and fix net/sheet references used by the PCB and BOM generation.
    [UTDRoboSubCompute.kicad_pcb, UTDRoboSubCompute.kicad_sch]
2026-02-21 cleaned up files
    [UTDRoboSubCompute.kicad_pcb]
2026-03-06 Better trace spacing, JLCPCB compliant & misc fixes
    - Added JLCPCB rules file
    - Made design JLCPCB compliant
    - updated README.md with additional details about diff and non-diff trace routing
    - updated images in README.md
    - updated clearance specs for signaling lines to 3*W
    - flipped GPIO header and reflected spacing changes in routing
    - Fixed Servo Address register floating pins issue
    - Fixed 3.3v input on SD power IC non-connection
    - rerouted servo PWM lines for better spacing
    - rerouted SD card data lines for better spacing, and clearer routes
    - Switched Servo Power Traces to fills in order to allow for multi-layer connections
    - added extra pads for bulk capacitors
    - added mor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
    [UTDRoboSubCompute.kicad_pcb, UTDRoboSubCompute.kicad_sch, cm5testcarrier.step]
2026-04-05 Added and adjusted decoupling caps
    - added decoupling capacitors to the USB IC
    - corrected the value of the center tap decoupling capacitor
    [UTDRoboSubCompute.kicad_pcb, UTDRoboSubCompute.kicad_sch, cm5testcarrier.step]
2026-04-05 Removed unneeded pull down
    Removed unnecessary pull down resistor on the OE pin of the Servo Controller. Since I am not folding out the output enable pin, a pull down is not needed
    [UTDRoboSubCompute.kicad_pcb, UTDRoboSubCompute.kicad_sch]
2026-04-11 Finished first verson
    - updated bom
    - added a more caps
    - changed value of resistor according to data sheet
    - updated ibom
    [10164227-1001A1RLF.stp, 150120GS75000.stp, 150120RS75000.stp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]

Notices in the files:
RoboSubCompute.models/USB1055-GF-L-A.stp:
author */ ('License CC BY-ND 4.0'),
